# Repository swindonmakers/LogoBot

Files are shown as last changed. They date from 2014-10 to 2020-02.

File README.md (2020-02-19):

LogoBot
=======

Cheap, extensible mobile robot design based on Arduino - inspired by Mirobot and others.  Many of the parts are 3D printed, using a tool-less pin system to connect to the base plate.  The non-printable *vitamins* are low-cost, common and globally available.

See the [Assembly Guides](http://rawgit.com/swindonmakers/LogoBot/master/hardware/docs/index.htm) for easy to follow build instructions and links to the printable STLs.

Developed by the Swindon Makerspace (UK) - see [LogoBot wiki page](https://github.com/swindonmakers/snhack.github.io/wiki/LogoBot) and [related Google Groups thread](https://groups.google.com/d/topic/swindon-hackspace/0EO_l_R9aW0/discussion)

Various photos of LogoBot builds can be found on the [Flickr group](https://www.flickr.com/groups/logobot/), please contribute if you build one!  Videos are collated in the [LogoBot youtube playlist](https://www.youtube.com/playlist?list=PLYuoVOMOzIhp9adQuXN-J07fskV5hSPBj).

Two of the variants are shown below - the basic design and the Scribbler variant that includes a pen lift:

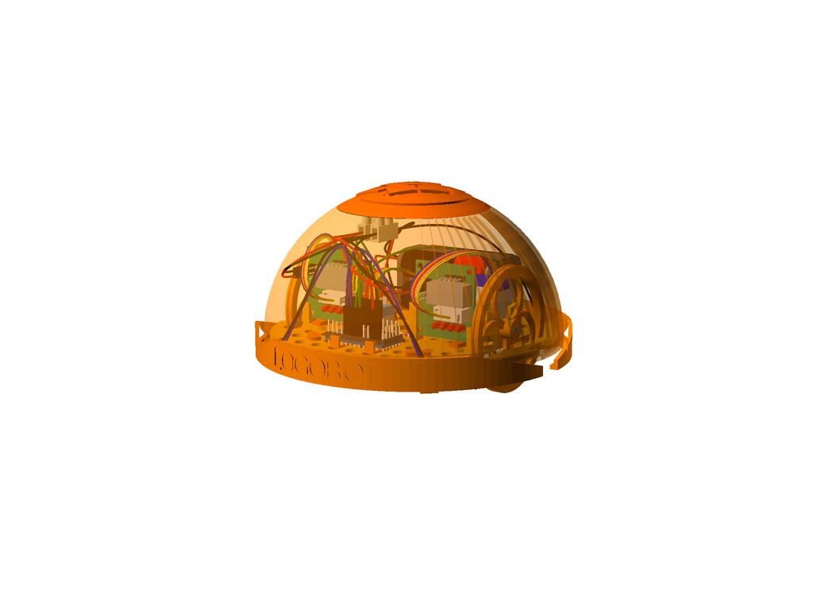
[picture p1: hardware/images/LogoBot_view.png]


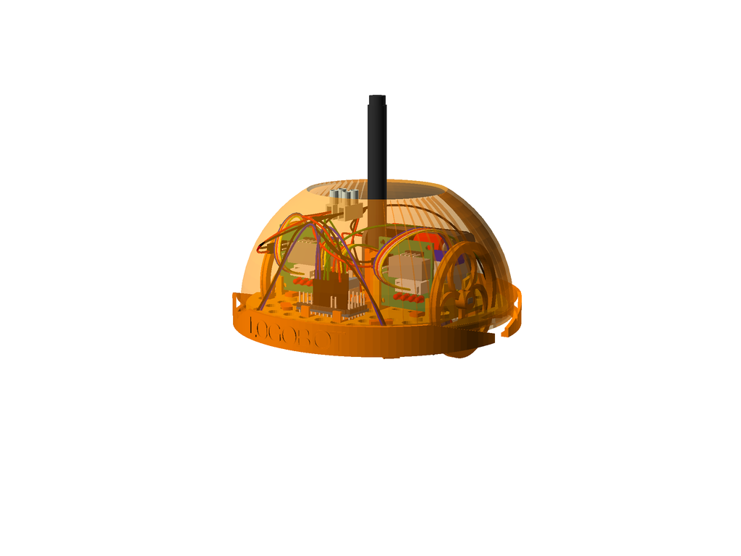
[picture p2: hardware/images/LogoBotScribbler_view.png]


Design Principles
-----------------

* Help teach electronics, programming, 3D design and 3D printing (both to ourselves and others)
* Highly interactive - to attract/hold attention
* Cheap (Total BOM <£20)
* Suitable for ages 6 - 100
* Simplicity is key - all parts/functionality must be easy to explain and understandable by 6-yr olds
* Solderless (where practical)
* Extensible - more sensors, more functionality
* Personalisable - we don't want lots of bland, generic little robots
* Include a Logo interpreter - as per it's namesake :)

File Structure
--------------

* hardware - all OpenSCAD models, and will contains electronic models in the future (e.g. PCB layout)
* software - firmwares and host implementations

Contributions
-------------

Development planning will be coordinated through the normal Wednesday meetings (i.e. who is working on what).  All project members will be given write access to the repo.

Design
------

The rest of this Wiki page is dedicated to design discussion, collected ideas, etc.  For the latest designs, guides and printable STLs, please refer to the [github site](https://github.com/swindonmakers/LogoBot).

Having discussed a variety configurations, we've settled on the following starter design:

* 2-wheels (stepper driven) with caster(s) - arranged as per traditional Turtle bot
* Front and rear bumpers, each connected to a pair of microswitches - users can choose to remap these switches to control behaviours and/or use them as bump switches
* An RGD LED to give the robot character, located near the top/centre of the robot
* A piezo sounder for audio feedback (R2D2 style noises?)

Scribbler
---------

The first standard extension will include a pen lift and WIFI module, permitting remote control from a phone or tablet using a LOGO command set.

* Central pen with micro-servo lift
* ESP8266-01 Wifi module

Other Extensions / Optional Extras
----------------------------------
* Bluetooth UART - for cable-free programming, inter-bot comms, host interface, etc
* Serial RGB LED (to reduce pin count)
* IR Reflectance sensors - for collision avoidance, cliff detection, line following, following behaviour, etc
* IR transceiver - for interaction with TV remotes and/or other robots
* Ultrasonic distance sensors - for collision avoidance, following behaviour, etc
* Speaker - for complex audio playback (e.g. WAV, MP3)
* Microphone(s) - for sound following/localisation and/or voice recognition/recording
* Light Sensors (LDR,etc) - following behaviour, etc
* Tilt sensor - for "I've fallen over" behaviour, etc

Customised Shell Ideas
----------------------
Although the reference design will include a basic dome shell, we really want makers to customise their LogoBot, and a custom shell is a quick way to make a big impression!  

Please add suggestions below, and if you start developing a design, then put your name in the Developer column and be sure to include a link to the source files (e.g. OpenSCAD file) - if there's lots of related information (pictures, etc), then create a wiki page for the design.

| Title | Developer | Link to Source | Notes |
| --- | --- | --- | --- |
| R2D2 | Jamie | | Just his head?  or perhaps a basic body as well? Matching program mode that drives piezo/speaker and adds R2 flourishes to movement (such as taking the 270° turn instead of 90°) |
| Dalek | | | Add a servo for the probiscus? | 
| Pumpkin | | | Halloween fun, with glowing eyes? |
| Lego Base | Damian | See Optional Extras | A lego plate lid to fit any of the standard shells |

Pin Assignments
---------------
First draft of pin assignments...  uses all the normal pins!

Pin(s) | Assignment
:----: | ----------
0-1    | Left spare for later addition of WIFI or Bluetooth UART
2-5    | Left stepper driver
6-9    | Right stepper driver
10     | Piezo sounder
11-13  | RGB LED
A0-A3  | Microswitches - Front Left, Front Right, Back Left, Back Right
|
A4-A7  | Spare headers, not usable on the breadboard

***A4-A7 are additional analog pins, not located at the edge of the board.***

See Also
--------
[OpenSCAD for Machine Design](https://github.com/swindonmakers/wiki/wiki/OpenSCAD-for-Machine-Design)

References
----------
* [Mirobot.io](http://mirobot.io/)
* [ProtoBot](http://www.thingiverse.com/thing:18264)
* [ScoutBot](http://www.thingiverse.com/thing:13042)
* [MiniSkybot](http://www.thingiverse.com/thing:7989)

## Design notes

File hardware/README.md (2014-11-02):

LogoBot Hardware
================

File Structure
--------------

**This Directory**

* LogoBot.scad - the complete reference robot design, open this in OpenSCAD to view the completed model

**Sub Directories**

* assemblies - contains the scad files that describe all the printable parts and sub-assemblies of LogoBot
* docs - assembly guides
* config - global scad configuration files
* printedparts - all printed parts
* utils - utility libraries to make modelling parts easier (e.g. extended shape libraries)
* vitamins - models of various non-printable vitamins (e.g. motors, switches, nuts, bolts)

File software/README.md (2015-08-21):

LogoBot Software
================

Contains the source for Arduino firmwares, ESP8266 firmwares and other bits (like the LogoBot Simulator)

File Structure
--------------
* [firmware](firmware) - contains the Arduino and ESP8266 firmwares and supporting libraries
* [simulator](simulator) - the web-based LogoBot Simulator

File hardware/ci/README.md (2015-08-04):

# CI Scripts

## Overview

The /hardware/ci directory contains all of the continuous integration scripts for the hardware portion of the project.

To build all files within the project:

1. Open a terminal and change to the /hardware/ci directory
2. Run: python build.py  (or just ./build.py)

### Build Process

The build.py script calls the other scripts in order to:

1. Check machine files (and all included files) for syntax errors
2. Parse the various machine files for BOM information, storing the result in hardware.json
3. Render STL and views for vitamins
4. Render STL and views for printed parts
5. Render views for each assembly step of the various assemblies
6. Render views for each completed machine
7. Generate an assembly guide for each machine, in both markdown and html
8. Generate a documentation index file, also in markdown and html
9. Generate a vitamin catalogue (markdown and html)

The process caches information about the structure of each part, so that only changes are rendered.

### Python Dependencies

You'll need to install the following dependencies to run the full build process:

1. PIL - the Python Image Library - use: pip install pillow
2. Pystache - the Pystache template library - use: pip install pystache

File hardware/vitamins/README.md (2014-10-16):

vitamins
========

This directory contains library modules for non-printable vitamin parts (e.g. motors, switches)

File Structure
--------------

**This Directory**

* PlasticCaster.scad - An example vitamin library that defines a basic plastic caster

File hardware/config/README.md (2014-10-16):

config
======

This directory contains .scad files that hold global configuration settings for the project.  Most of these files require little editing and form part of the machine design pattern.

File Structure
--------------

**This Directory**

* assemblies.scad - A list of included assembly files
* colors.scad - A set of material colors for use in vitamins and assemblies
* config.scad - Master config file, includes all other config files - include this in the machine file (e.g. /LogoBot.scad)
* **machine.scad** - Machine specific variables - this is where all of the LogoBot specific parameters are held
* utils.scad - A list of included utility files
* vitamins.scad - A list of included vitamin files

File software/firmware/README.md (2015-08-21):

# firmware

This directory contains the Arduino and ESP8266 firmwares and supporting libraries.
The source files are well commented and should be fairly self-explanatory.

## Build Notes

To build the various firmwares, set your Arduino IDE Sketchbook path to point to this (firmware) directory (restart required).  The various sketches can then be loaded from the File -> Sketchbook menu.

To easily program the ESP8266 firmwares, you'll need need Arduino IDE v1.6.4 or newer.  Then add ESP support via Board Manager.  Testing has been done using ESP8266-01 modules, but other variants should work as well.

## Contents
--------------
* libraries - various reusable libraries for developing LogoBot firmwares, some 3rd party
* LogoBotBasic - Arduino firmware for the basic LogoBot - start here!
* LogoBotEsp8266 - ESP8266 firmware to complement the LogoBotWifiScribbler firmware
* LogoBotIRSeeker - Arduino firmware for the IR Seeker variant
* LogoBotLineFollower - Arduino firmware for the Line Follower variant
* LogoBotPolarGraph - Arduino firmware for the Polar Graph variant
* LogoBotWifiScribbler - Arduino firmware for the Scribbler variant

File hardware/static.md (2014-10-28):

# Static Analysis Report

## Summary

**Fit to Publish:** Yes

Section    | OK  | Note | Warning | Error
---------- |:---:|:----:|:-------:|:-----:
[Assemblies](#assemblies) | 29  | 0    | 1       | 0    
[Vitamins  ](#vitamins  ) | 44  | 0    | 12      | 0    
**Total**  | **73**  | **0**  | **13**  | **0** 

## Assemblies

File     | OK | Note | Warning | Error
------  | :---:  | :---:  | :---:  | :---: 
[Wheel.scad](#wheelscad) | 6 | 0 | 0 | 0
[MarbleCaster.scad](#marblecasterscad) | 6 | 0 | 0 | 0
[Shell.scad](#shellscad) | 5 | 0 | 1 | 0
[Breadboard.scad](#breadboardscad) | 6 | 0 | 0 | 0
[LogoBot.scad](#logobotscad) | 6 | 0 | 0 | 0
**Total**  | **29**  | **0**  | **1**  | **0** 

### Shell.scad

* **Warnings**
  * 2 supplementary modules do not comply with naming convention (BasicShell_STL, BasicShell_STL_View)

## Vitamins

File     | OK | Note | Warning | Error
------  | :---:  | :---:  | :---:  | :---: 
[ULN2003DriverBoard.scad](#uln2003driverboardscad) | 4 | 0 | 0 | 0
[Marble.scad](#marblescad) | 4 | 0 | 0 | 0
[MicroUSB.scad](#microusbscad) | 3 | 0 | 1 | 0
[LED.scad](#ledscad) | 4 | 0 | 0 | 0
[BatteryPack.scad](#batterypackscad) | 2 | 0 | 2 | 0
[motor.scad](#motorscad) | 1 | 0 | 3 | 0
[Bolt.scad](#boltscad) | 2 | 0 | 2 | 0
[MicroSwitch.scad](#microswitchscad) | 3 | 0 | 1 | 0
[Breadboard.scad](#breadboardscad) | 4 | 0 | 0 | 0
[MicroServo.scad](#microservoscad) | 4 | 0 | 0 | 0
[PlasticCaster.scad](#plasticcasterscad) | 4 | 0 | 0 | 0
[JumperWire.scad](#jumperwirescad) | 4 | 0 | 0 | 0
[ArduinoPro.scad](#arduinoproscad) | 4 | 0 | 0 | 0
[murata-piezos.scad](#murata-piezosscad) | 1 | 0 | 3 | 0
**Total**  | **44**  | **0**  | **12**  | **0** 

### MicroUSB.scad

* **Warnings**
  * Vitamin module name does not match filename

### BatteryPack.scad

* **Warnings**
  * Vitamin module name does not match filename
  * 3 supplementary modules do not comply with naming convention (battery, battery_pack_linear, battery_pack_double)

### motor.scad

* **Warnings**
  * Filename is not in UpperCamelCase
  * Vitamin module name does not match filename
  * 1 supplementary modules do not comply with naming convention (logo_motor)

### Bolt.scad

* **Warnings**
  * Vitamin module name does not match filename
  * 3 supplementary modules do not comply with naming convention (HexHeadScrew, HexHeadBolt, Nut)

### MicroSwitch.scad

* **Warnings**
  * 1 supplementary modules do not comply with naming convention (terminal)

### murata-piezos.scad

* **Warnings**
  * Filename is not in UpperCamelCase
  * Vitamin module name does not match filename
  * 25 supplementary modules do not comply with naming convention (murata_7BB_12_9, murata_7BB_15_6, murata_7BB_20_3, murata_7BB_20_6, murata_7BB_20_6L0, murata_7BB_27_4, murata_7BB_27_4L0, murata_7BB_35_3, murata_7BB_35_3L0, murata_7BB_41_2, murata_7BB_41_2L0, murata_7NB_31R2_1, murata_7BB_20_6C, murata_7BB_20_6CL0, murata_7BB_27_4C, murata_7BB_27_4CL0, murata_7BB_35_3C, murata_7BB_35_3CL0, murata_7BB_41_2C, murata_7BB_41_2CL0, murata_7SB_34R7_3C, murata_7series, murata_PKM12EPYH4002_B0, murata_PKM17EPP_2002_B0, murata_PKM_cyl_type)

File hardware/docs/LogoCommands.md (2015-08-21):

## LogoBot - Logo Command Reference

###  Movement

Command | Example | Description
--- | --- | --- 
FD <dist> | FD 20 | Drive forward 20mm | 
BK <dist> | BK 20 | Drive backwards 20mm | 
LT <ang> | LT 90 | Turn left 90 degrees | 
RT <ang> | RT 45 | Turn right 45 degrees | 
TO <x> <y> | TO 20 45 | Move to position x=20, y=45 |
ARC <x> <y> | ARC 50 50 | Move in an arc to position x=50, y=50 |
CIRC <dia> <dir> | CIRC 100 1 | Move in a circle of radius 100 in an anticlockwise direction (<dir>=1 for anticlockwise, -1 for clockwise) |
CS | CS | "Clear screen" - resets current position to be x=0, y=0 |
ST | ST | Smoothly stop movement |
SE | SE | Emergency stop |

###  Other

Command | Example | Description
--- | --- | --- 
PU | PU | Pen up |
PD | PD | Pen down |
BZ <ms> | BZ 500 | Sound the buzzer for 500 milliseconds |
PF <ms> | PF 500 | Pause for 500 milliseconds |

### Text

Command | Example | Description
--- | --- | --- 
WT <msg> | WT Hello | Writes "Hello" |
FS <size> | FS 20 | Sets font size to 20 (default) |
SIG | SIG | Signs Logobots name |

### Debug

Command | Example | Description
--- | --- | --- 
PQ | PQ | Prints the current command queue to serial console for debugging |

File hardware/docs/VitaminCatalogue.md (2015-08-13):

# Vitamin Catalogue

### Contents
 * [ArduinoPro.scad ](#arduinoproscad)
 * [Battery.scad ](#batteryscad)
 * [BatteryPack.scad ](#batterypackscad)
 * [Breadboard.scad ](#breadboardscad)
 * [ESP8266.scad ](#esp8266scad)
 * [FTDIBreakout.scad ](#ftdibreakoutscad)
 * [HCSR04UltrasonicSensor.scad ](#hcsr04ultrasonicsensorscad)
 * [HookAndLoopTape.scad ](#hookandlooptapescad)
 * [JumperWire.scad ](#jumperwirescad)
 * [LED.scad ](#ledscad)
 * [LineSensor.scad ](#linesensorscad)
 * [Marble.scad ](#marblescad)
 * [MicroServo.scad ](#microservoscad)
 * [MicroSwitch.scad ](#microswitchscad)
 * [MiniToggleSwitch.scad ](#minitoggleswitchscad)
 * [Pen.scad ](#penscad)
 * [ServoHorn.scad ](#servohornscad)
 * [TerminalBlock.scad ](#terminalblockscad)
 * [ULN2003DriverBoard.scad ](#uln2003driverboardscad)
 * [nut.scad ](#nutscad)
 * [screw.scad ](#screwscad)
 * [washer.scad ](#washerscad)

## ArduinoPro.scad

Title | Call | Image
--- | --- | ---
Arduino Pro Mini No Header Pins, no serial pins | `ArduinoPro(type=ArduinoPro_Mini, headerpins=0,serialpins=0)` | Arduino Pro Mini No Header Pins, no serial pins

## Battery.scad

Title | Call | Image
--- | --- | ---
AA Battery | `Battery(Battery_AA)` | AA Battery

## BatteryPack.scad

Title | Call | Image
--- | --- | ---
Battery Pack | `BatteryPack()` | Battery Pack

## Breadboard.scad

Title | Call | Image
--- | --- | ---
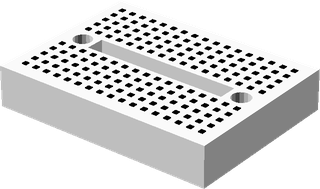
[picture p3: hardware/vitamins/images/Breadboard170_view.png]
Breadboard 170
Breadboard 170 | `Breadboard(Breadboard_170)` | 

## ESP8266.scad

Title | Call | Image
--- | --- | ---
ESP8266 01 | `ESP8266(ESP8266_01)` | ESP8266 01

## FTDIBreakout.scad

Title | Call | Image
--- | --- | ---
FTDI Breakout | `FTDIBreakout()` | FTDI Breakout

## HCSR04UltrasonicSensor.scad

Title | Call | Image
--- | --- | ---
HCSR04 Ultrasonic Sensor | `HCSR04UltrasonicSensor()` | HCSR04 Ultrasonic Sensor

## HookAndLoopTape.scad

Title | Call | Image
--- | --- | ---
Hook and Loop Tape 40x25mm | `HookAndLoopTape(length=40, width=25)` | Hook and Loop Tape 40x25mm

## JumperWire.scad

Title | Call | Image
--- | --- | ---
JumperWire None to None 1pin 100mm | `JumperWire(type=JumperWire_NN1, length=100)` | JumperWire None to None 1pin 100mm
JumperWire Female to None 1pin 100mm | `JumperWire(type=JumperWire_FN1, length=100)` | JumperWire Female to None 1pin 100mm
JumperWire Male to Male 2pin 100mm | `JumperWire(type=JumperWire_MM2, length=100)` | JumperWire Male to Male 2pin 100mm
JumperWire Female to Female 2pin 100mm | `JumperWire(type=JumperWire_FF2, length=100)` | JumperWire Female to Female 2pin 100mm
JumperWire Male to Female 2pin 100mm | `JumperWire(type=JumperWire_MF2, length=100)` | JumperWire Male to Female 2pin 100mm
JumperWire Female to Female 3pin 100mm | `JumperWire(type=JumperWire_FF3, length=100)` | JumperWire Female to Female 3pin 100mm
JumperWire Female to Female 4pin 100mm | `JumperWire(type=JumperWire_FF4, length=100)` | JumperWire Female to Female 4pin 100mm
JumperWire Female to Male 4pin 100mm | `JumperWire(type=JumperWire_FM4, length=100)` | JumperWire Female to Male 4pin 100mm

## LED.scad

Title | Call | Image
--- | --- | ---
3mm LED | `LED(LEDType=LED_3mm)` | 3mm LED
5mm LED | `LED(LEDType=LED_5mm)` | 5mm LED
RGB_5mm LED | `LED(LEDType=LED_RGB_5mm)` | RGB_5mm LED

## LineSensor.scad

Title | Call | Image
--- | --- | ---
Line Sensor | `LineSensor()` | Line Sensor

## Marble.scad

Title | Call | Image
--- | --- | ---
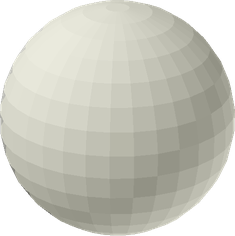
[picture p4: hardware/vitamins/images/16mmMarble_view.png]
16mm Marble
16mm Marble | `Marble(Marble_16mm)` | 

## MicroServo.scad

Title | Call | Image
--- | --- | ---
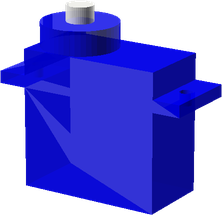
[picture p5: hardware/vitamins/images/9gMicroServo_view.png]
9g Micro Servo
9g Micro Servo | `MicroServo()` | 

## MicroSwitch.scad

Title | Call | Image
--- | --- | ---
MicroSwitch | `MicroSwitch()` | MicroSwitch

## MiniToggleSwitch.scad

Title | Call | Image
--- | --- | ---
SPST6A Mini Toggle Switch | `MiniToggleSwitch(MiniToggleSwitch_SPST6A)` | SPST6A Mini Toggle Switch

## Pen.scad

Title | Call | Image
--- | --- | ---
Fine Line Pen | `Pen()` | Fine Line Pen

## ServoHorn.scad

Title | Call | Image
--- | --- | ---
Servo Horn | `ServoHorn()` | Servo Horn

## TerminalBlock.scad

Title | Call | Image
--- | --- | ---
2 Pole 20A Terminal Block | `TerminalBlock(type=TerminalBlock_20A,poles=2)` | 2 Pole 20A Terminal Block

## ULN2003DriverBoard.scad

Title | Call | Image
--- | --- | ---
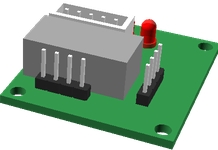
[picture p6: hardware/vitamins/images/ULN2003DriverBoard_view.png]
ULN2003 Driver Board
ULN2003 Driver Board | `ULN2003DriverBoard()` | 

## nut.scad

Title | Call | Image
--- | --- | ---
M2 Nut | `nut(type=M2_nut,nyloc=false,brass=false )` | M2 Nut
M2.5 Nut | `nut(type=M2p5_nut,nyloc=false,brass=false )` | M2.5 Nut
M3 Nut | `nut(type=M3_nut,nyloc=false,brass=false )` | M3 Nut
M4 Nut | `nut(type=M4_nut,nyloc=false,brass=false )` | M4 Nut
M5 Nut | `nut(type=M5_nut,nyloc=false,brass=false )` | M5 Nut
M6 Nut | `nut(type=M6_nut,nyloc=false,brass=false )` | M6 Nut
M6 Half Nut | `nut(type=M6_half_nut,nyloc=false,brass=false )` | M6 Half Nut
M8 Nut | `nut(type=M8_nut,nyloc=false,brass=false )` | M8 Nut
M10 Nut | `nut(type=M10_nut,nyloc=false,brass=false )` | M10 Nut

## screw.scad

Title | Call | Image
--- | --- | ---
M2 pan screw x 20mm | `screw(type=M2_pan_screw,length=20, hob_point=0 )` | M2 pan screw x 20mm
M2.5 pan screw x 20mm | `screw(type=M2p5_pan_screw,length=20, hob_point=0 )` | M2.5 pan screw x 20mm
M2.5 cap screw x 20mm | `screw(type=M2p5_cap_screw,length=20, hob_point=0 )` | M2.5 cap screw x 20mm
M3 cap screw x 20mm | `screw(type=M3_cap_screw,length=20, hob_point=0 )` | M3 cap screw x 20mm
M3 pan screw x 20mm | `screw(type=M3_pan_screw,length=20, hob_point=0 )` | M3 pan screw x 20mm
M3 hex screw x 20mm | `screw(type=M3_hex_screw,length=20, hob_point=0 )` | M3 hex screw x 20mm
M3 grub screw x 20mm | `screw(type=M3_grub_screw,length=20, hob_point=0 )` | M3 grub screw x 20mm
M4 cap screw x 20mm | `screw(type=M4_cap_screw,length=20, hob_point=0 )` | M4 cap screw x 20mm
M4 pan screw x 20mm | `screw(type=M4_pan_screw,length=20, hob_point=0 )` | M4 pan screw x 20mm
M4 hex screw x 20mm | `screw(type=M4_hex_screw,length=20, hob_point=0 )` | M4 hex screw x 20mm
M4 grub screw x 20mm | `screw(type=M4_grub_screw,length=20, hob_point=0 )` | M4 grub screw x 20mm
M5 cap screw x 20mm | `screw(type=M5_cap_screw,length=20, hob_point=0 )` | M5 cap screw x 20mm
M6 cap screw x 20mm | `screw(type=M6_cap_screw,length=20, hob_point=0 )` | M6 cap screw x 20mm
M6 selftap screw T25 x 20mm | `screw(type=M6_selftap_screw,length=20, hob_point=0 )` | M6 selftap screw T25 x 20mm
M8 cap screw x 20mm | `screw(type=M8_cap_screw,length=20, hob_point=0 )` | M8 cap screw x 20mm
M8 hex screw x 20mm | `screw(type=M8_hex_screw,length=20, hob_point=0 )` | M8 hex screw x 20mm
M10 cap screw x 20mm | `screw(type=M10_cap_screw,length=20, hob_point=0 )` | M10 cap screw x 20mm
M5 low profile screw x 20mm | `screw(type=M5_lowprofile_screw,length=20, hob_point=0 )` | M5 low profile screw x 20mm
No2 pan wood screw x 20mm | `screw(type=No2_screw,length=20, hob_point=0 )` | No2 pan wood screw x 20mm
No4 pan wood screw x 20mm | `screw(type=No4_screw,length=20, hob_point=0 )` | No4 pan wood screw x 20mm
No6 pan wood screw x 20mm | `screw(type=No6_screw,length=20, hob_point=0 )` | No6 pan wood screw x 20mm
No6 cs  wood screw x 20mm | `screw(type=No6_cs_screw,length=20, hob_point=0 )` | No6 cs wood screw x 20mm
6-32 pan screw x 20mm | `screw(type=No632_pan_screw,length=20, hob_point=0 )` | 6-32 pan screw x 20mm

## washer.scad

Title | Call | Image
--- | --- | ---
M2 Washer 6x0.5 | `washer(type=M2_washer)` | M2 Washer 6x0.5
M2.5 Washer 5.9x0.5 | `washer(type=M2p5_washer)` | M2.5 Washer 5.9x0.5
M3 Washer 7x0.5 | `washer(type=M3_washer)` | M3 Washer 7x0.5
M3.5 Washer 8x0.5 | `washer(type=M3p5_washer)` | M3.5 Washer 8x0.5
M4 Washer 9x0.8 | `washer(type=M4_washer)` | M4 Washer 9x0.8
M5 Washer 10x1 | `washer(type=M5_washer)` | M5 Washer 10x1
M5 Washer 20x1.4 | `washer(type=M5_penny_washer)` | M5 Washer 20x1.4
M6 Washer 12x1.5 | `washer(type=M6_washer)` | M6 Washer 12x1.5
M8 Washer 17x1.8 | `washer(type=M8_washer)` | M8 Washer 17x1.8
M8 Washer 30x1.5 | `washer(type=M8_penny_washer)` | M8 Washer 30x1.5
M10 Washer 21x2.2 | `washer(type=M10_washer)` | M10 Washer 21x2.2
M3 Rubber Washer 10x1.5 | `washer(type=M3_rubber_washer)` | M3 Rubber Washer 10x1.5

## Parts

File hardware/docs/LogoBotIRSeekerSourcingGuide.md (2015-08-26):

# LogoBot IR Seeker
# Sourcing Guide

### 1x Arduino Pro Mini Pins on top, inc serial pins

Unit Cost | Source | Notes 
--- | --- | --- 
3 | [link](http://www.aliexpress.com/item/CP2102-Module-Pro-Mini-Module-Atmega328-3-3V-8M-For-Arduinoi-Compatible-With-Nano-Free-Shipping/2002847394.html) | Use 3.3v version for wider compatibility and longer battery life

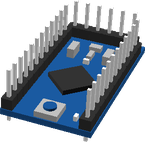
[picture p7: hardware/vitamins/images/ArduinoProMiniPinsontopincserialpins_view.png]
 

### 4x AA Battery

Unit Cost | Source | Notes 
--- | --- | --- 
0.35 | All over the place | Use rechargeables to save cost

 

### 1x Battery Pack

Unit Cost | Source | Notes 
--- | --- | --- 
0.49 | [link](http://www.aliexpress.com/item/Black-Color-2-2-AA-Battery-1-5V-Holder-Storage-Boxes-for-DIY-Experiment-Test-Cascade/1981330624.html) | Any 4xAA pack should work fine, or use 2S LIPO, NIMH, NICAD, etc

 

### 1x Hook and Loop Tape 40x10mm

Unit Cost | Source | Notes 
--- | --- | --- 
0.2 | Hardware store | 

 

### 2x JumperWire Female to Female 4pin 100mm

Unit Cost | Source | Notes 
--- | --- | --- 
0.05 | [link](http://www.ebay.co.uk/itm/40pcs-10cm-Dupont-Female-to-Female-Jumper-Wire-Ribbon-Cable-Pi-Pic-Breadboard-/281423655999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) | Buy in bulk x40

 

### 6x JumperWire Female to None 1pin 100mm

Unit Cost | Source | Notes 
--- | --- | --- 
0.05 |  | Chop end off normal jumper

 

### 4x JumperWire Female to None 1pin 70mm

Unit Cost | Source | Notes 
--- | --- | --- 
0.05 |  | Chop end off normal jumper

 

### 4x JumperWire None to None 1pin 100mm

Unit Cost | Source | Notes 
--- | --- | --- 
0.05 |  | Use any thin multi-strand or solid core wire

 

### 3x JumperWire None to None 1pin 50mm

Unit Cost | Source | Notes 
--- | --- | --- 
0.05 |  | Use any thin multi-strand or solid core wire

 

### 8x 3mm LED

No sources found

 

### 1x 16mm Marble

Unit Cost | Source | Notes 
--- | --- | --- 
0.13 | [link](http://www.ebay.co.uk/itm/NEW-50-16mm-MARBLES-PLUS-ONE-DOBBER-SHOOTER-MARBLE-GREEN-ACK-D60069-/371035484158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) | Buy in bulk x50

 

### 1x 9g Micro Servo

No sources found

 

### 4x MicroSwitch

Unit Cost | Source | Notes 
--- | --- | --- 
0.13 | [link](http://www.ebay.co.uk/itm/15Pcs-SPDT-Straight-Hinge-Lever-Momentary-Micro-Switch-AC125V-1A-/291501876300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) | Buy in bulk x15

 

### 1x SPST6A Mini Toggle Switch

Unit Cost | Source | Notes 
--- | --- | --- 
0.56 | [link](http://www.ebay.co.uk/itm/10x-Mini-Toggle-Switch-6A-SPST-ON-OFF-/251443706793?) | Buy in bulk x10

 

### 1x Servo Horn

No sources found

 

### 1x Sharp2Y0A21

No sources found

 

### 2x 28YBJ48 Stepper Motor

Unit Cost | Source | Notes 
--- | --- | --- 
1.76 | [link](http://www.aliexpress.com/item/5V-Stepper-Motor-28BYJ-48-With-Drive-Test-Module-Board-ULN2003-5-Line-4-Phase-free/1436201179.html) | Comes with driver board

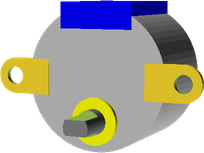
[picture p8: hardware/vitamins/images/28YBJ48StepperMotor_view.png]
 

### 1x 2 Pole 20A Terminal Block

Unit Cost | Source | Notes 
--- | --- | --- 
0.2 | Hardware store | Break off from long terminal strip

 

### 2x ULN2003 Driver Board

Unit Cost | Source | Notes 
--- | --- | --- 
0 |  | Ordered with motor

 

## Summary

### Total Costs

Metric | Value 
--- | --- 
Total Vitamins | 48
Total Cost (cheapest) | 10.97 GBP

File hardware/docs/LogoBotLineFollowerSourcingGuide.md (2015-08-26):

# LogoBot Line Follower
# Sourcing Guide

### 1x Arduino Pro Mini Pins on top, inc serial pins

Unit Cost | Source | Notes 
--- | --- | --- 
3 | [link](http://www.aliexpress.com/item/CP2102-Module-Pro-Mini-Module-Atmega328-3-3V-8M-For-Arduinoi-Compatible-With-Nano-Free-Shipping/2002847394.html) | Use 3.3v version for wider compatibility and longer battery life

 

### 4x AA Battery

Unit Cost | Source | Notes 
--- | --- | --- 
0.35 | All over the place | Use rechargeables to save cost

 

### 1x Battery Pack

Unit Cost | Source | Notes 
--- | --- | --- 
0.49 | [link](http://www.aliexpress.com/item/Black-Color-2-2-AA-Battery-1-5V-Holder-Storage-Boxes-for-DIY-Experiment-Test-Cascade/1981330624.html) | Any 4xAA pack should work fine, or use 2S LIPO, NIMH, NICAD, etc

 

### 1x Hook and Loop Tape 40x10mm

Unit Cost | Source | Notes 
--- | --- | --- 
0.2 | Hardware store | 

 

### 2x JumperWire Female to Female 4pin 100mm

Unit Cost | Source | Notes 
--- | --- | --- 
0.05 | [link](http://www.ebay.co.uk/itm/40pcs-10cm-Dupont-Female-to-Female-Jumper-Wire-Ribbon-Cable-Pi-Pic-Breadboard-/281423655999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) | Buy in bulk x40

 

### 4x JumperWire Female to None 1pin 100mm

Unit Cost | Source | Notes 
--- | --- | --- 
0.05 |  | Chop end off normal jumper

 

### 4x JumperWire Female to None 1pin 70mm

Unit Cost | Source | Notes 
--- | --- | --- 
0.05 |  | Chop end off normal jumper

 

### 2x JumperWire None to None 1pin 100mm

Unit Cost | Source | Notes 
--- | --- | --- 
0.05 |  | Use any thin multi-strand or solid core wire

 

### 3x JumperWire None to None 1pin 50mm

Unit Cost | Source | Notes 
--- | --- | --- 
0.05 |  | Use any thin multi-strand or solid core wire

 

### 8x 3mm LED

No sources found

 

### 2x Line Sensor

No sources found

 

### 1x 16mm Marble

Unit Cost | Source | Notes 
--- | --- | --- 
0.13 | [link](http://www.ebay.co.uk/itm/NEW-50-16mm-MARBLES-PLUS-ONE-DOBBER-SHOOTER-MARBLE-GREEN-ACK-D60069-/371035484158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) | Buy in bulk x50

 

### 1x SPST6A Mini Toggle Switch

Unit Cost | Source | Notes 
--- | --- | --- 
0.56 | [link](http://www.ebay.co.uk/itm/10x-Mini-Toggle-Switch-6A-SPST-ON-OFF-/251443706793?) | Buy in bulk x10

 

### 2x 28YBJ48 Stepper Motor

Unit Cost | Source | Notes 
--- | --- | --- 
1.76 | [link](http://www.aliexpress.com/item/5V-Stepper-Motor-28BYJ-48-With-Drive-Test-Module-Board-ULN2003-5-Line-4-Phase-free/1436201179.html) | Comes with driver board

 

### 1x 2 Pole 20A Terminal Block

Unit Cost | Source | Notes 
--- | --- | --- 
0.2 | Hardware store | Break off from long terminal strip

 

### 2x ULN2003 Driver Board

Unit Cost | Source | Notes 
--- | --- | --- 
0 |  | Ordered with motor

 

## Summary

### Total Costs

Metric | Value 
--- | --- 
Total Vitamins | 39
Total Cost (cheapest) | 10.25 GBP

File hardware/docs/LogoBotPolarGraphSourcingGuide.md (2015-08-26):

# LogoBot Polar Graph
# Sourcing Guide

### 1x Arduino Pro Mini Pins on top, inc serial pins

Unit Cost | Source | Notes 
--- | --- | --- 
3 | [link](http://www.aliexpress.com/item/CP2102-Module-Pro-Mini-Module-Atmega328-3-3V-8M-For-Arduinoi-Compatible-With-Nano-Free-Shipping/2002847394.html) | Use 3.3v version for wider compatibility and longer battery life

 

### 8x 3mm LED

No sources found

 

### 3x 16mm Marble

Unit Cost | Source | Notes 
--- | --- | --- 
0.13 | [link](http://www.ebay.co.uk/itm/NEW-50-16mm-MARBLES-PLUS-ONE-DOBBER-SHOOTER-MARBLE-GREEN-ACK-D60069-/371035484158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) | Buy in bulk x50

 

### 1x 9g Micro Servo

No sources found

 

### 1x Fine Line Pen

No sources found

 

### 1x Servo Horn

No sources found

 

### 2x 28YBJ48 Stepper Motor

Unit Cost | Source | Notes 
--- | --- | --- 
1.76 | [link](http://www.aliexpress.com/item/5V-Stepper-Motor-28BYJ-48-With-Drive-Test-Module-Board-ULN2003-5-Line-4-Phase-free/1436201179.html) | Comes with driver board

 

### 2x ULN2003 Driver Board

Unit Cost | Source | Notes 
--- | --- | --- 
0 |  | Ordered with motor

 

### 4x No6 cs  wood screw x 20mm

No sources found

 

## Summary

### Total Costs

Metric | Value 
--- | --- 
Total Vitamins | 23
Total Cost (cheapest) | 6.91 GBP

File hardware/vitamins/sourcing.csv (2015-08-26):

Vitamin | Cost | Source | Notes
Arduino Pro Mini Pins on top, inc serial pins | 3 | http://www.aliexpress.com/item/CP2102-Module-Pro-Mini-Module-Atmega328-3-3V-8M-For-Arduinoi-Compatible-With-Nano-Free-Shipping/2002847394.html | Use 3.3v version for wider compatibility and longer battery life
AA Battery | 0.35 | All over the place | Use rechargeables to save cost
Battery Pack | 0.49 | http://www.aliexpress.com/item/Black-Color-2-2-AA-Battery-1-5V-Holder-Storage-Boxes-for-DIY-Experiment-Test-Cascade/1981330624.html | Any 4xAA pack should work fine, or use 2S LIPO, NIMH, NICAD, etc
Hook and Loop Tape 40x10mm | 0.2 | Hardware store
JumperWire Female to Female 4pin 100mm | 0.05 | http://www.ebay.co.uk/itm/40pcs-10cm-Dupont-Female-to-Female-Jumper-Wire-Ribbon-Cable-Pi-Pic-Breadboard-/281423655999 | Buy in bulk x40
JumperWire Female to None 1pin 100mm | 0.05 |  | Chop end off normal jumper
JumperWire Female to None 1pin 70mm | 0.05 |  | Chop end off normal jumper
JumperWire None to None 1pin 100mm | 0.05 |  | Use any thin multi-strand or solid core wire
JumperWire None to None 1pin 50mm | 0.05 |  | Use any thin multi-strand or solid core wire
16mm Marble | 0.13 | http://www.ebay.co.uk/itm/NEW-50-16mm-MARBLES-PLUS-ONE-DOBBER-SHOOTER-MARBLE-GREEN-ACK-D60069-/371035484158 | Buy in bulk x50
MicroSwitch | 0.13 | http://www.ebay.co.uk/itm/15Pcs-SPDT-Straight-Hinge-Lever-Momentary-Micro-Switch-AC125V-1A-/291501876300 | Buy in bulk x15
SPST6A Mini Toggle Switch | 0.56 | http://www.ebay.co.uk/itm/10x-Mini-Toggle-Switch-6A-SPST-ON-OFF-/251443706793? | Buy in bulk x10
28YBJ48 Stepper Motor | 1.76 | http://www.aliexpress.com/item/5V-Stepper-Motor-28BYJ-48-With-Drive-Test-Module-Board-ULN2003-5-Line-4-Phase-free/1436201179.html | Comes with driver board
2 Pole 20A Terminal Block | 0.2 | Hardware store | Break off from long terminal strip
ULN2003 Driver Board | 0 |  | Ordered with motor

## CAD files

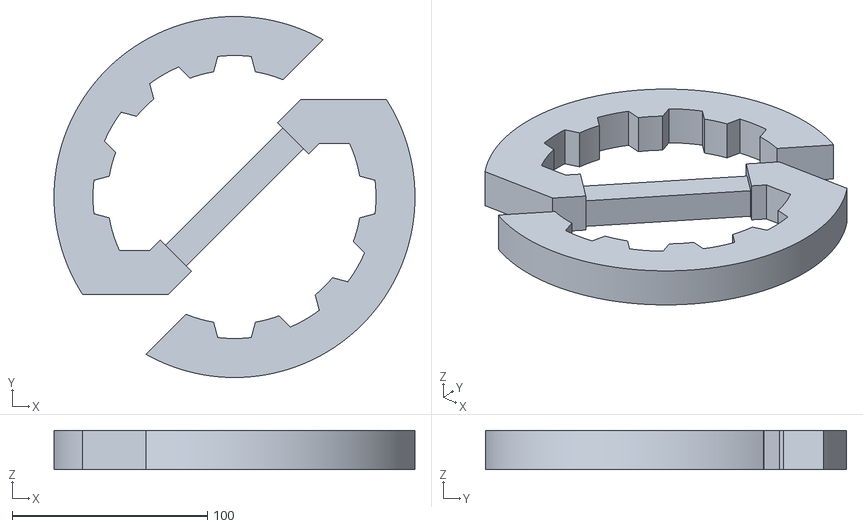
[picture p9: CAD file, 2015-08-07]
hardware/printedparts/snhack_logo_s.stl
185.0 x 185.0 x 20.0

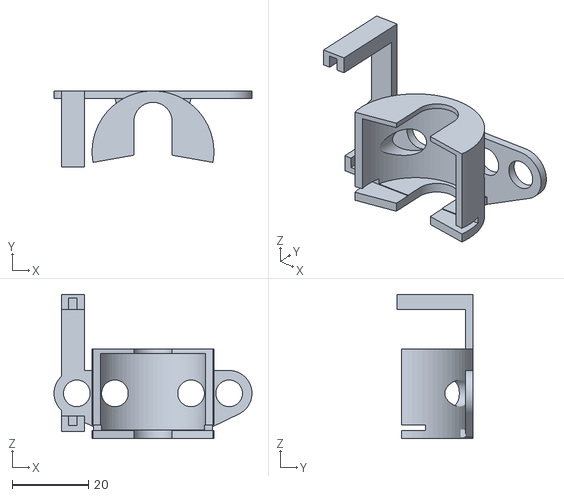
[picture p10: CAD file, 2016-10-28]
hardware/printedparts/stl/LeftMotorClip.stl
52.0 x 20.0 x 37.9

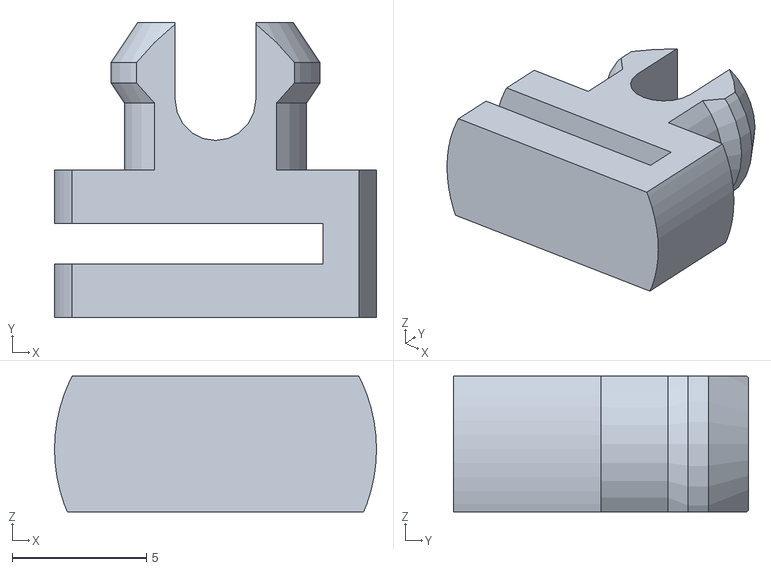
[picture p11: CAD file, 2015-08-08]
hardware/sandbox/stl/PinsCableClipDev.stl
12.0 x 11.0 x 5.05

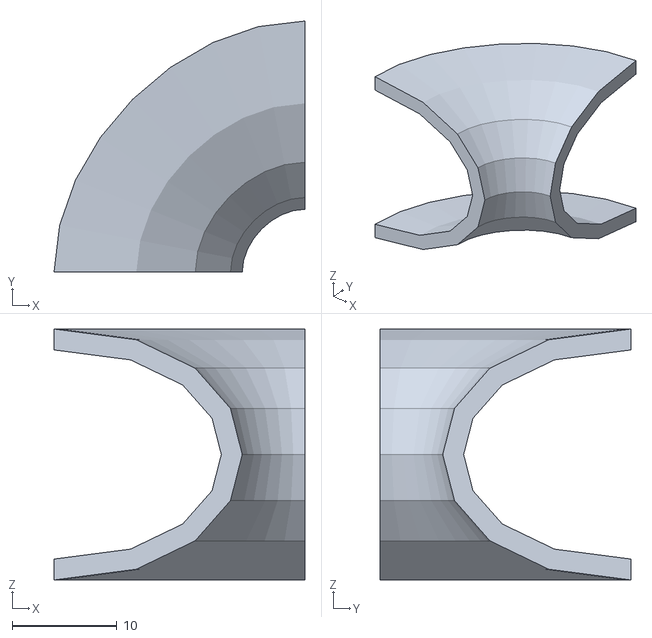
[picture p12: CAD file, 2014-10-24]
hardware/utils/surfacesolids/curve_section.stl
24.0 x 24.0 x 24.0

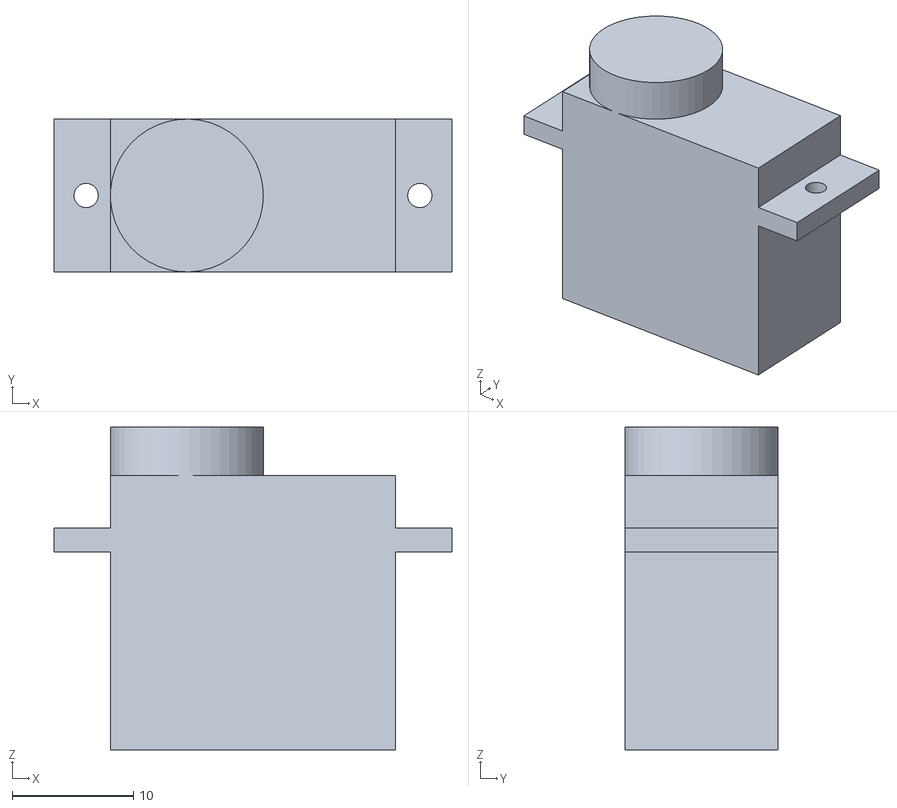
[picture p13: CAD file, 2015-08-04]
hardware/vitamins/stl/MicroServo_Body.stl
32.8 x 12.6 x 26.6

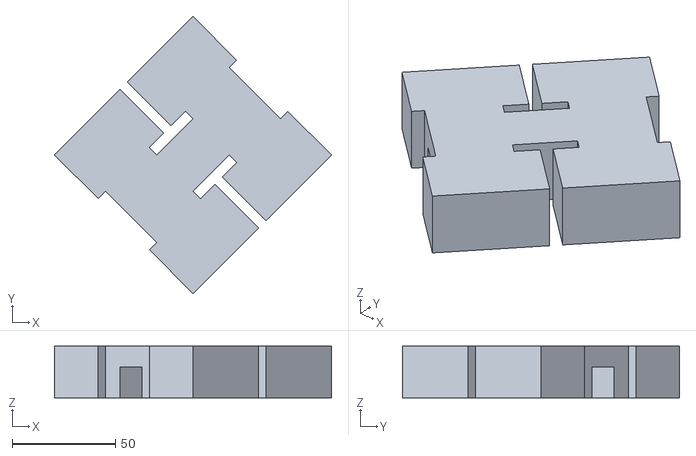
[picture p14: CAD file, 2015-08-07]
hardware/printedparts/snhack_logo_h.stl
134.4 x 134.4 x 25.0

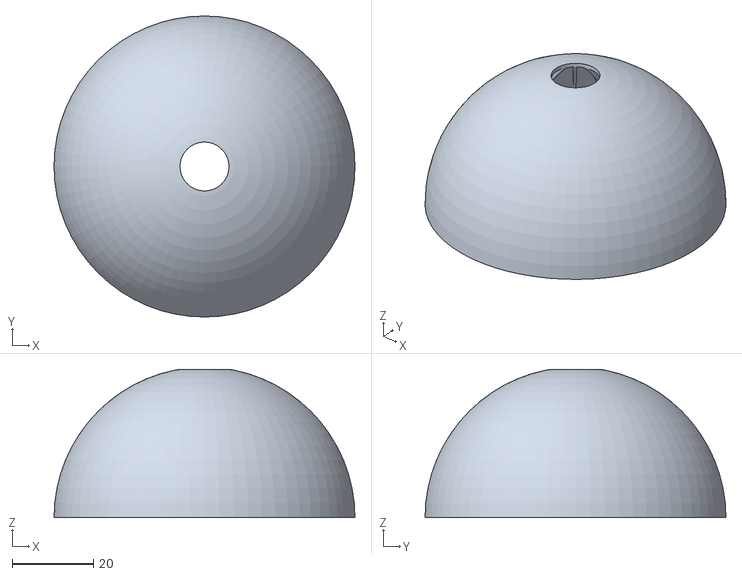
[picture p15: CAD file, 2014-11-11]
hardware/sandbox/stl/supported_dome_70mm.stl
74.0 x 74.0 x 36.5

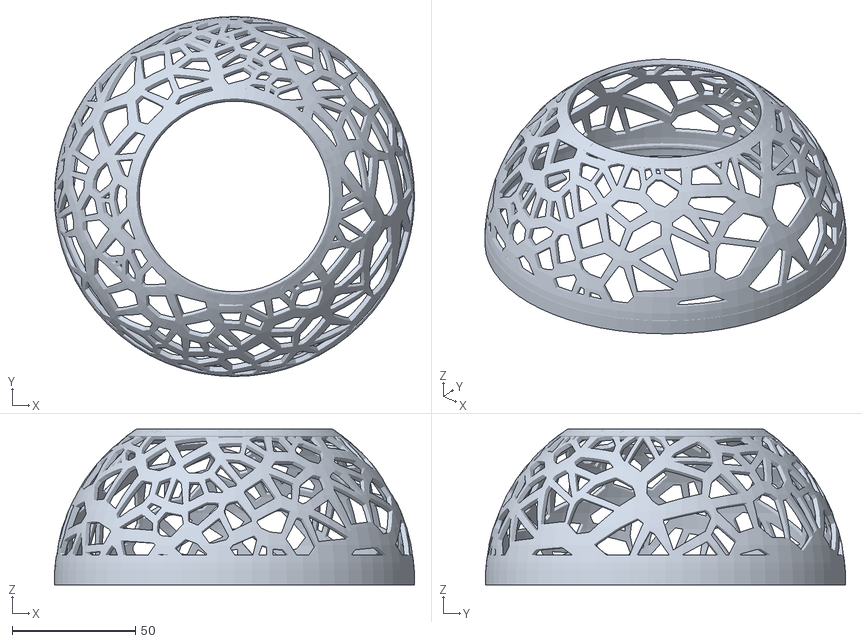
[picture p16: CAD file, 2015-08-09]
hardware/sandbox/VoronoiShell3.stl
146.0 x 146.0 x 63.2

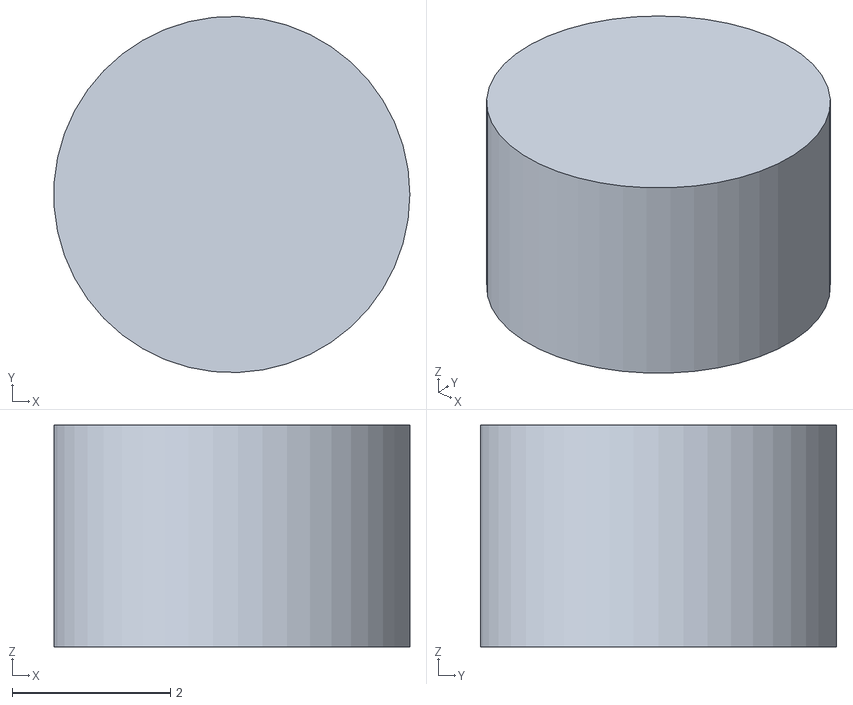
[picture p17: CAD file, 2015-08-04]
hardware/vitamins/stl/MicroServo_Spline.stl
4.49 x 4.50 x 2.80

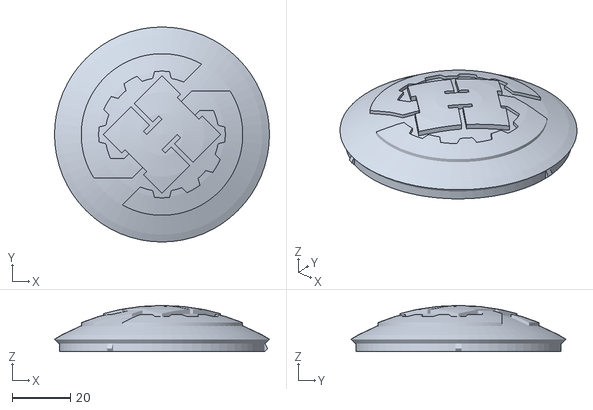
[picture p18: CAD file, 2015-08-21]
hardware/printedparts/stl/Lid.stl
73.9 x 73.9 x 15.9

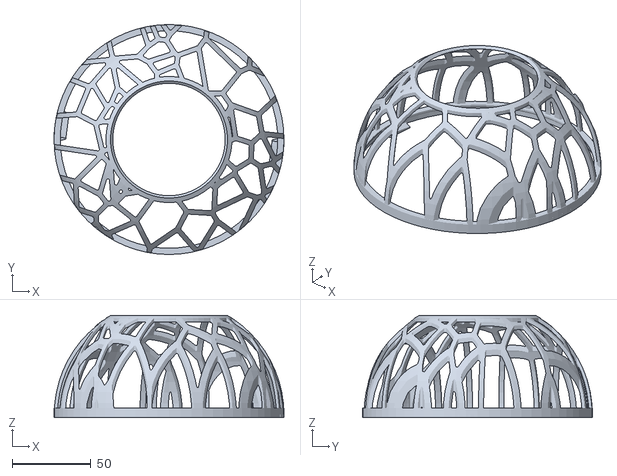
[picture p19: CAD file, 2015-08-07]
hardware/sandbox/VoronoiShell.stl
146.0 x 146.0 x 64.8

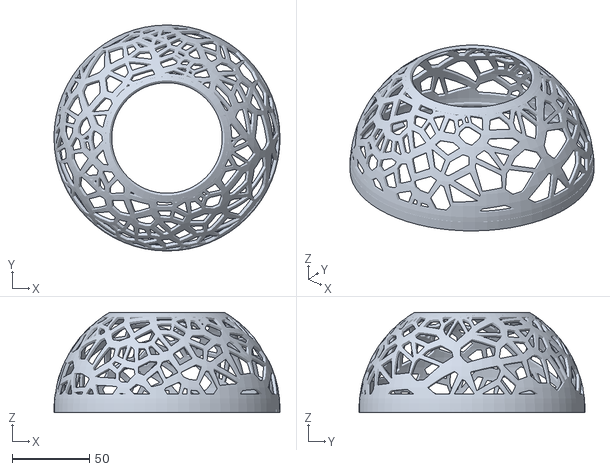
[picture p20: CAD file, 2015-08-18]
hardware/printedparts/stl/VoronoiShellType2.stl
146.0 x 146.0 x 64.8

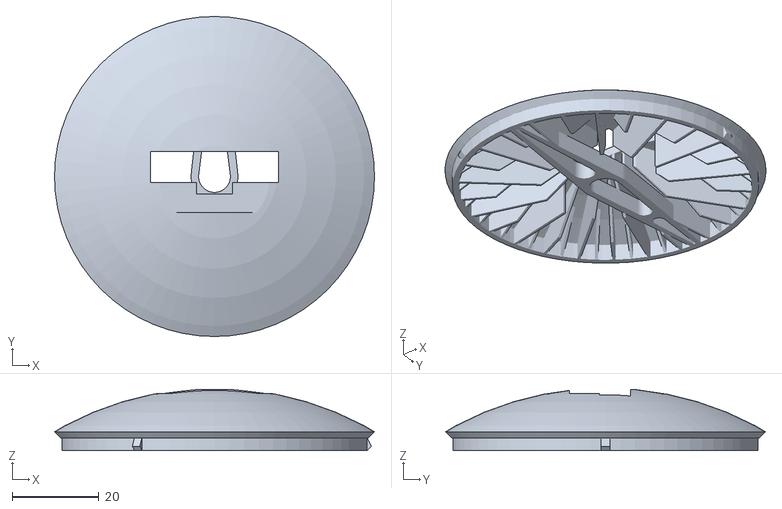
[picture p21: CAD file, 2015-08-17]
hardware/printedparts/stl/LidIR.stl
73.6 x 73.6 x 14.1

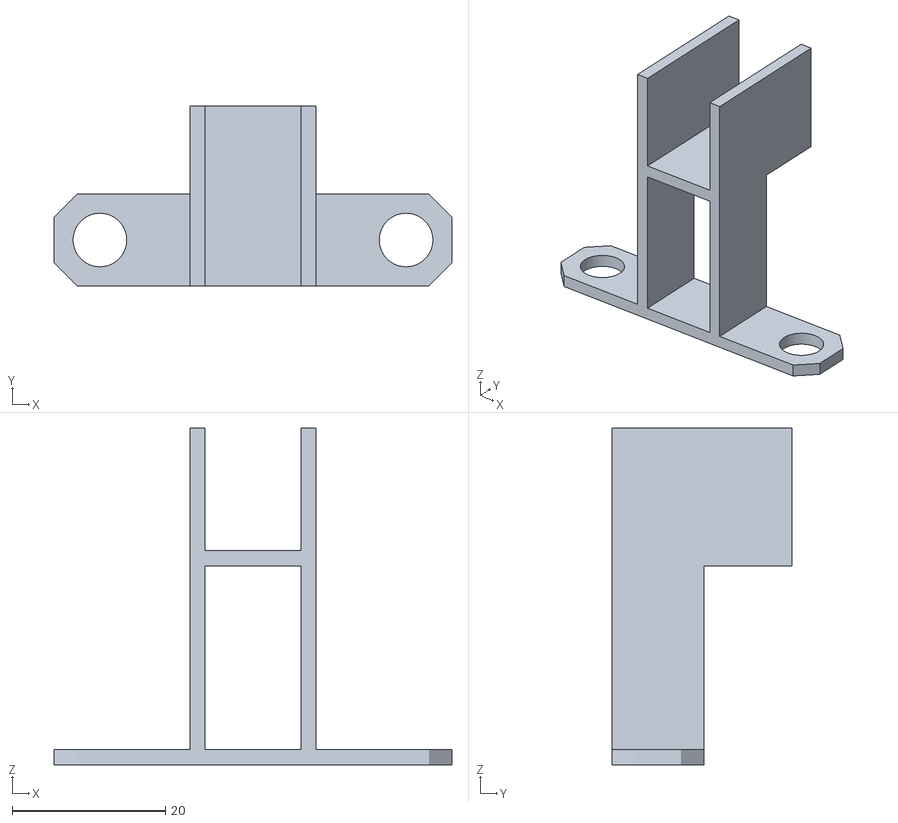
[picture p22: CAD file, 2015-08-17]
hardware/printedparts/stl/IRServoBracket.stl
52.0 x 23.5 x 44.0

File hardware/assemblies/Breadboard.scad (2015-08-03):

/*
	Assembly: BreadboardAssembly
	Breadboard assembly - includes Arduino and fixings

	Local Frame:
		Origin

*/

// Connectors
// ----------

module BreadboardAssembly() {

    assembly("assemblies/Breadboard.scad", "Brain", str("BreadboardAssembly()")) {

        if (DebugCoordinateFrames) frame();

        // debug connectors?
        if (DebugConnectors) {

        }

        // Vitamins
        // --------

        // Breadboard
        Breadboard(Breadboard_170);

        // Arduino
        step(1,
                "Push the Arduino onto the breadboard - make sure you position it correctly,
                 as it's a tight fit with the Robot base!") {
            view(t=[21,17,9], r=[62,0,218], d=316);

            attachWithOffset(Breadboard_Con_Pin(Breadboard_170, along=3, across=7, ang=90), DefConDown, [0,0,3]) {
                ArduinoPro(ArduinoPro_Micro, ArduinoPro_Pins_Opposite);
            }
        }

	}
}

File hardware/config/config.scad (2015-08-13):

//
// Config
//

// Coding-style
// ------------
//
// Global variables are written in UpperCamelCase.
// A logical hierarchy should be indicated using underscores, for example:
//     StepperMotor_Connections_Axle
//
// Global short-hand references should be kept to a minimum to avoid name-collisions



// Global OpenSCAD variables - short-hand!
//
eta = 0.01;                     // small fudge factor to stop CSG barfing on coincident faces.
$fa = 5;
$fs = 0.5;


// Printer specific parameters
//
Perim = 0.5;    // perim extrusion width for 0.2 or 0.3 layer height
Layers = 0.3;
2Perim = 2*Perim;
4Perim = 4*Perim;

// short-hand
perim = Perim;
layers = Layers;
2perim = 2Perim;
4perim = 4Perim;


// Debugging

DebugConnectors = 1;  			// set to 1 to debug, set to 0 for production
DebugCoordinateFrames = 1; 		// set to 1 to debug, set to 0 for production


// Visualisation

// set to true to use STL for printed parts rather than rendering on the fly
UseSTL = false;
STLPath = "../printedparts/stl/";
UseVitaminSTL = true;
VitaminSTL = "../vitamins/stl/";

$Explode  = false;
$ShowStep = 100;

$DefaultViewSize = [400, 300];


// Include all other configuration files

include <holesizes.scad>
include <colors.scad>
include <utils.scad>
include <vitamins.scad>
include <machine.scad>
include <printedparts.scad>
include <assemblies.scad>

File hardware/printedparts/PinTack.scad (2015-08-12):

// Connectors

PinTack_Con_Def = [[0,0,0], [0,0,-1], 0,0,0];


module PinTack_STL(h=10) {

    printedPart(
        "printedparts/PinTack.scad",
        str("Pin Tack H",h),
        str("PinTack_STL(h=",h,")")
    ) {
        markdown("guide","Orient to print on the flat side, no brim.  You may need to sand the flat sides depending on the tolerances of your printer.");

        view(t=[0,0,0],r=[145,135,0],d=130);

        if (DebugCoordinateFrames) frame();
        if (DebugConnectors) {
            connector(PinTack_Con_Def);
        }

        color(Level3PlasticColor) {
            // uses pins.scad library:
            pintack(h=h, bh=2, lh=2, r=PinDiameter/2-0.1);
        }
    }
}

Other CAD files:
hardware/printedparts/stl/RightMotorClip.stl
hardware/printedparts/stl/PinTackH65.stl
hardware/printedparts/stl/LegoLid.stl
hardware/printedparts/stl/CasterHousing.stl
hardware/utils/pins.scad
hardware/LogoBot.scad
hardware/LogoBotIRSeeker.scad
hardware/LogoBotLineFollower.scad
hardware/LogoBotPolarGraph.scad
hardware/LogoBotScribbler.scad
hardware/OptionalExtras.scad
hardware/assemblies/Bumper.scad
hardware/assemblies/Capstan.scad
hardware/assemblies/Gondola.scad
hardware/assemblies/LidIR.scad
hardware/assemblies/LineSensor.scad
hardware/assemblies/LogoBot.scad
hardware/assemblies/LogoBotIRSeeker.scad
hardware/assemblies/LogoBotLineFollower.scad
hardware/assemblies/LogoBotPolarGraph.scad
hardware/assemblies/MarbleCaster.scad
hardware/assemblies/PenLift.scad
hardware/assemblies/Shell.scad
hardware/assemblies/Wheel.scad
hardware/ci/assemblies.scad
hardware/ci/assembly.scad
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

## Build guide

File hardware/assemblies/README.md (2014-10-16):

assemblies
==========

This directory contains the core of the design.  Each file describes a sub-assembly and any associated printed parts.

File Naming Convention
----------------------

Each file should contain a single assembly and it's associated printed parts.
Name files in same case as the assembly module it contains, without the Assembly suffix.

File Structure
--------------

**This Directory**

* LogoBot.scad - the master assembly of the complete robot

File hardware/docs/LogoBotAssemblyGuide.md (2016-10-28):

# LogoBot
# Assembly Guide

view

## Bill of Materials

Make sure you have all of the following parts before you begin.

### Vitamins

Qty | Vitamin | Image
--- | --- | ---
1 | [Arduino Pro Mini Pins on top, inc serial pins]() |  | 
4 | [AA Battery]() |  | 
1 | [Battery Pack]() |  | 
1 | [Hook and Loop Tape 40x10mm]() |  | 
2 | [JumperWire Female to Female 4pin 100mm]() |  | 
6 | [JumperWire Female to None 1pin 100mm]() |  | 
4 | [JumperWire Female to None 1pin 70mm]() |  | 
4 | [JumperWire None to None 1pin 100mm]() |  | 
3 | [JumperWire None to None 1pin 50mm]() |  | 
8 | [3mm LED]() |  | 
1 | [16mm Marble]() |  | 
4 | [MicroSwitch]() |  | 
1 | [SPST6A Mini Toggle Switch]() |  | 
2 | [28YBJ48 Stepper Motor]() |  | 
1 | [2 Pole 20A Terminal Block]() |  | 
2 | [ULN2003 Driver Board]() |  | 

### Printed Parts

Qty | Part Name | Image
--- | --- | ---
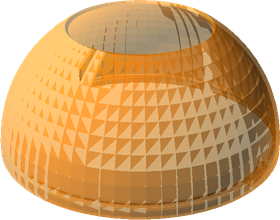
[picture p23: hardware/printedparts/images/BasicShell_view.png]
1 | [Basic Shell](../printedparts/stl/BasicShell.stl) |  | 
2 | [BumperStabiliser](../printedparts/stl/BumperStabiliser.stl) |  | 
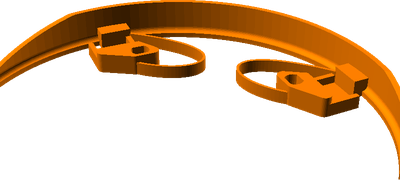
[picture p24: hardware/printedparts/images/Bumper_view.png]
2 | [Bumper](../printedparts/stl/Bumper.stl) |  | 
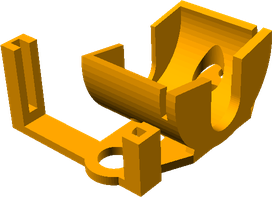
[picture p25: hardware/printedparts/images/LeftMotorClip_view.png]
1 | [Left Motor Clip](../printedparts/stl/LeftMotorClip.stl) |  | 
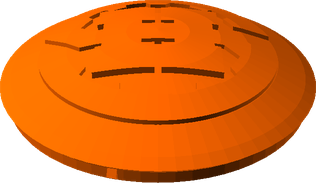
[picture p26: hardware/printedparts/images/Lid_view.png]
1 | [Lid](../printedparts/stl/Lid.stl) |  | 
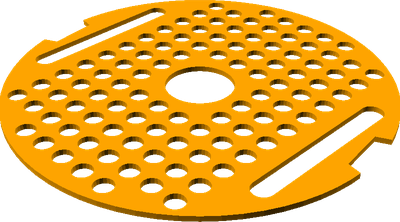
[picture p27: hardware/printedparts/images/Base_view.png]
1 | [Base](../printedparts/stl/Base.stl) |  | 
1 | [Caster Housing](../printedparts/stl/CasterHousing.stl) |  | 
4 | [Pin Tack H14.1](../printedparts/stl/PinTackH141.stl) |  | 
1 | [Pin Tack H6.1](../printedparts/stl/PinTackH61.stl) |  | 
4 | [Pin Tack H7](../printedparts/stl/PinTackH7.stl) |  | 
2 | [Pro Mini Clip](../printedparts/stl/ProMiniClip.stl) |  | 
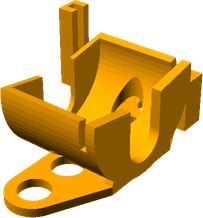
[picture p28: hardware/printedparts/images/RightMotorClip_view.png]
1 | [Right Motor Clip](../printedparts/stl/RightMotorClip.stl) |  | 
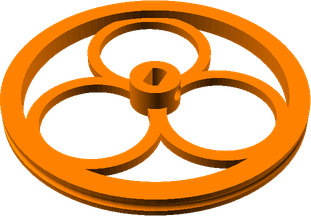
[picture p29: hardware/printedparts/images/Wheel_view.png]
2 | [Wheel](../printedparts/stl/Wheel.stl) |  | 

**Plastic Required**

153.8cm3, 0.19KG,  approx: 2.5 GBP

# Assembly Instructions

## Bumpers (x2)

### Vitamins

Qty | Vitamin | Image
--- | --- | ---
4 | [MicroSwitch]() |  | 

### Printed Parts

Qty | Part Name | Image
--- | --- | ---
2 | [Bumper](../printedparts/stl/Bumper.stl) |  | 

### Assembly Animation

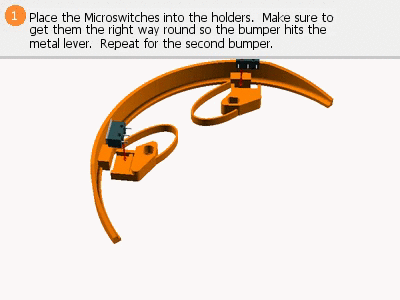
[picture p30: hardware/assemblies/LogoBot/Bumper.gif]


### Assembly Steps

1. Place the Microswitches into the holders.  Make sure to get them the right way round so the bumper hits the metal lever.  Repeat for the second bumper.
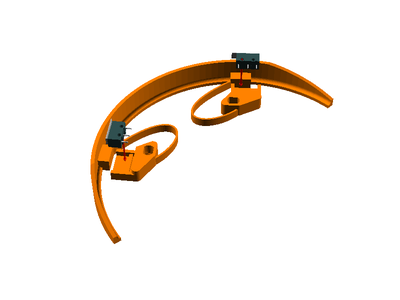
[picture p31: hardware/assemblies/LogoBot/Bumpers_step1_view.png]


## Left Drive Wheel

### Vitamins

Qty | Vitamin | Image
--- | --- | ---
1 | [28YBJ48 Stepper Motor]() |  | 
1 | [ULN2003 Driver Board]() |  | 

### Printed Parts

Qty | Part Name | Image
--- | --- | ---
1 | [Left Motor Clip](../printedparts/stl/LeftMotorClip.stl) |  | 
2 | [Pin Tack H7](../printedparts/stl/PinTackH7.stl) |  | 
1 | [Wheel](../printedparts/stl/Wheel.stl) |  | 

### Assembly Animation

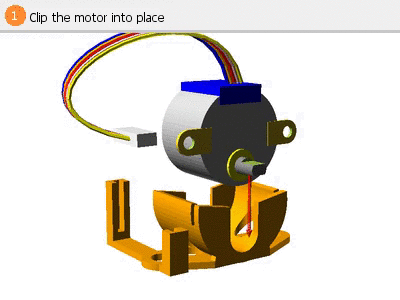
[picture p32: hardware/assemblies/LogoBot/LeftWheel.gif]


### Assembly Steps

1. Clip the motor into place
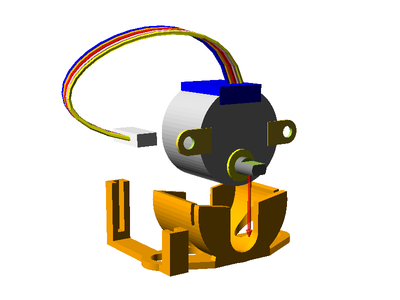
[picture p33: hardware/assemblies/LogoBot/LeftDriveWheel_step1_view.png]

2. Push the pins into the motor clip
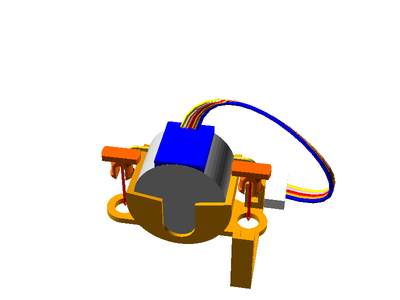
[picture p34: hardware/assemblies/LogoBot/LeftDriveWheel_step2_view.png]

3. Push the wheel onto the motor shaft, then add a rubber band or o-ring to the wheel for extra grip.  You can also add a retaining grub screw if necessary.
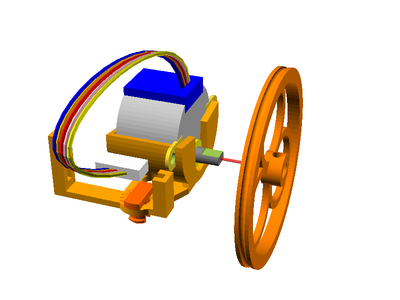
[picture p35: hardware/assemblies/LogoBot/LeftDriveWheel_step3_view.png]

4. Slide the stepper driver into place and plug in the cable for the motor
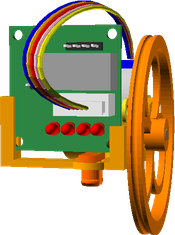
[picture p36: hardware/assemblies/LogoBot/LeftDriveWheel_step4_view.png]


## Right Drive Wheel

### Vitamins

Qty | Vitamin | Image
--- | --- | ---
1 | [28YBJ48 Stepper Motor]() |  | 
1 | [ULN2003 Driver Board]() |  | 

### Printed Parts

Qty | Part Name | Image
--- | --- | ---
2 | [Pin Tack H7](../printedparts/stl/PinTackH7.stl) |  | 
1 | [Right Motor Clip](../printedparts/stl/RightMotorClip.stl) |  | 
1 | [Wheel](../printedparts/stl/Wheel.stl) |  | 

### Assembly Animation

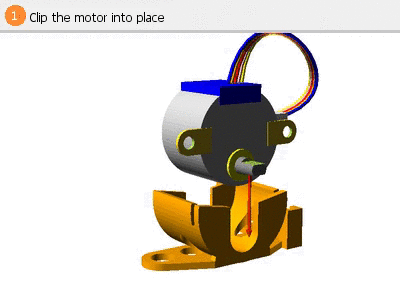
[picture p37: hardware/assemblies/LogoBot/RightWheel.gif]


### Assembly Steps

1. Clip the motor into place
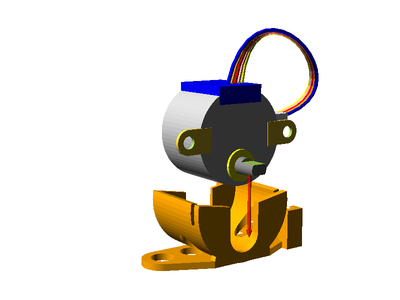
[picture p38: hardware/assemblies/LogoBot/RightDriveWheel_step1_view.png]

2. Push the pins into the motor clip
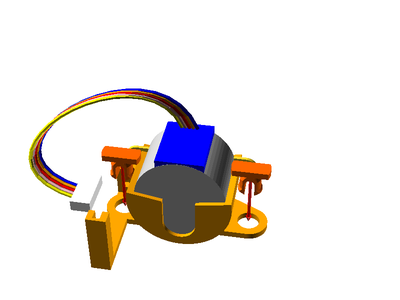
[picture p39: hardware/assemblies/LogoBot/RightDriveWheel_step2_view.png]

3. Push the wheel onto the motor shaft, then add a rubber band or o-ring to the wheel for extra grip.  You can also add a retaining grub screw if necessary.
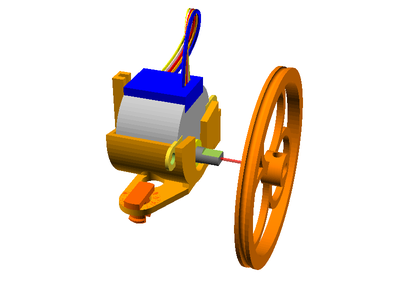
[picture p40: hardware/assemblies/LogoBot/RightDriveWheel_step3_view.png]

4. Slide the stepper driver into place and plug in the cable for the motor
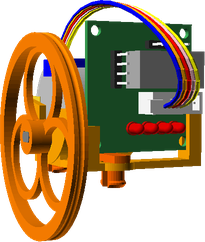
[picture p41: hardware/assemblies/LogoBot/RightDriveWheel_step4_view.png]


## Rear Caster

### Vitamins

Qty | Vitamin | Image
--- | --- | ---
1 | [16mm Marble]() |  | 

### Printed Parts

Qty | Part Name | Image
--- | --- | ---
1 | [Caster Housing](../printedparts/stl/CasterHousing.stl) |  | 

### Assembly Animation

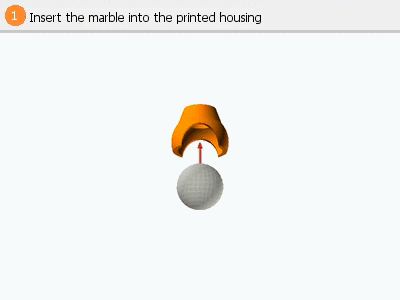
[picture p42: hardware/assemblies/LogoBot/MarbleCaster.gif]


### Assembly Steps

1. Insert the marble into the printed housing
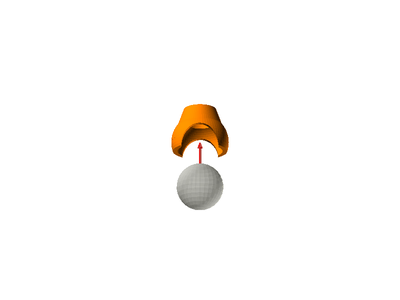
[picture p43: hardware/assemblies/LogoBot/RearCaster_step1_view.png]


## Shell

### Printed Parts

Qty | Part Name | Image
--- | --- | ---
1 | [Basic Shell](../printedparts/stl/BasicShell.stl) |  | 
1 | [Lid](../printedparts/stl/Lid.stl) |  | 

### Assembly Animation

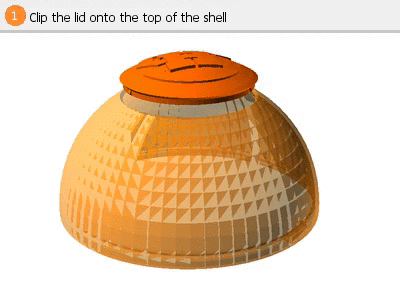
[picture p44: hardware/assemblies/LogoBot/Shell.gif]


### Assembly Steps

1. Clip the lid onto the top of the shell
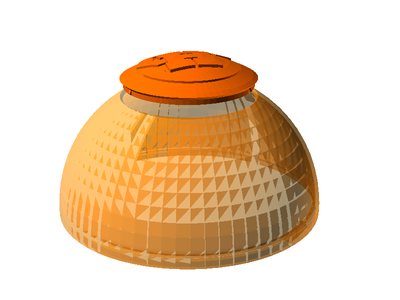
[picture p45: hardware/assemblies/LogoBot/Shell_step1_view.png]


## Final Assembly

### Vitamins

Qty | Vitamin | Image
--- | --- | ---
1 | [Arduino Pro Mini Pins on top, inc serial pins]() |  | 
4 | [AA Battery]() |  | 
1 | [Battery Pack]() |  | 
1 | [Hook and Loop Tape 40x10mm]() |  | 
2 | [JumperWire Female to Female 4pin 100mm]() |  | 
6 | [JumperWire Female to None 1pin 100mm]() |  | 
4 | [JumperWire Female to None 1pin 70mm]() |  | 
4 | [JumperWire None to None 1pin 100mm]() |  | 
3 | [JumperWire None to None 1pin 50mm]() |  | 
1 | [SPST6A Mini Toggle Switch]() |  | 
1 | [2 Pole 20A Terminal Block]() |  | 

### Printed Parts

Qty | Part Name | Image
--- | --- | ---
2 | [BumperStabiliser](../printedparts/stl/BumperStabiliser.stl) |  | 
1 | [Base](../printedparts/stl/Base.stl) |  | 
4 | [Pin Tack H14.1](../printedparts/stl/PinTackH141.stl) |  | 
1 | [Pin Tack H6.1](../printedparts/stl/PinTackH61.stl) |  | 
2 | [Pro Mini Clip](../printedparts/stl/ProMiniClip.stl) |  | 

### Sub-Assemblies

Qty | Name 
--- | --- 
2 | Bumpers
1 | Left Drive Wheel
1 | Right Drive Wheel
1 | Rear Caster
1 | Shell

### Assembly Animation



### Assembly Steps

1. Plug the Pro Mini Clips into the base and then snap the Arduino Pro Mini into them
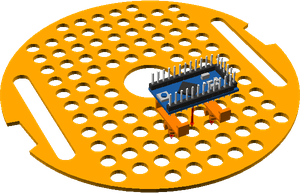
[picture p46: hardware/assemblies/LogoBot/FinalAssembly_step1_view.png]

2. Connect the two bumper assemblies using four of the push pins with flat heads
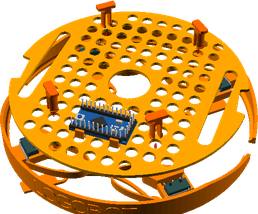
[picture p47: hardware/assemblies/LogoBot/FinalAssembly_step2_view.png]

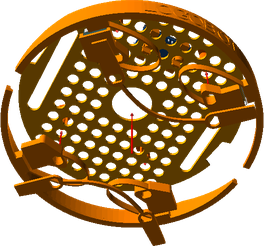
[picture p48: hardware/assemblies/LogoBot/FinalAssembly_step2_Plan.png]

4. Plug the two wheels assemblies into the base
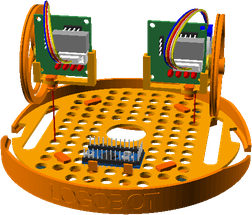
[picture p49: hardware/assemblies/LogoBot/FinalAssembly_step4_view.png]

5. Connect the jumper wires between the motor drivers and the Arduino
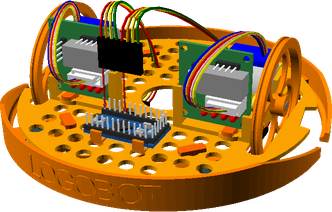
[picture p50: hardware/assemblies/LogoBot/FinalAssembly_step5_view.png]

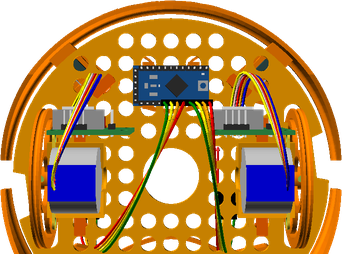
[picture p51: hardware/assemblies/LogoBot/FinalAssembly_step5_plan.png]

6. Fix the power toggle switch into place
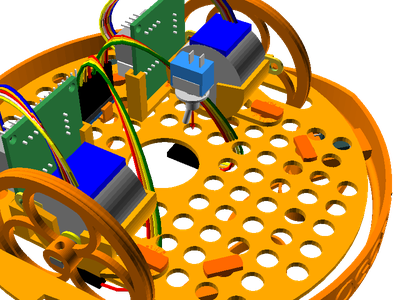
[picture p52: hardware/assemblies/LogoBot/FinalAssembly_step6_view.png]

9. Align the caster assembly with the base, then insert a short pin to lock it to the base
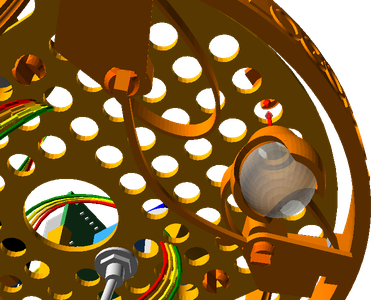
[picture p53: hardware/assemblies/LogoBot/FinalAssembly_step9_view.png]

11. Attach the battery pack with self-adhesive hook and loop tape
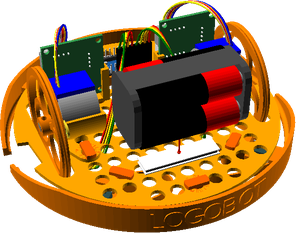
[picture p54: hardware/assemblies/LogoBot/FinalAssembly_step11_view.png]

12. Wire in the terminal block to distribute power
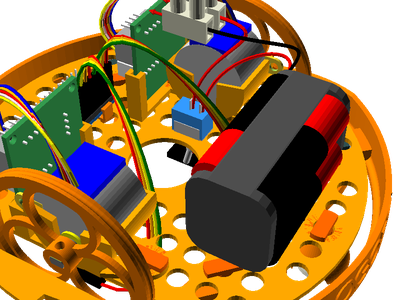
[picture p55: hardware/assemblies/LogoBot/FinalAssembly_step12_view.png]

13. Wire up power to the stepper drivers and Arduino.  Then connect the microswitches to the Arduino. 
            Refer to the following wiring for Arduino pin connections: 
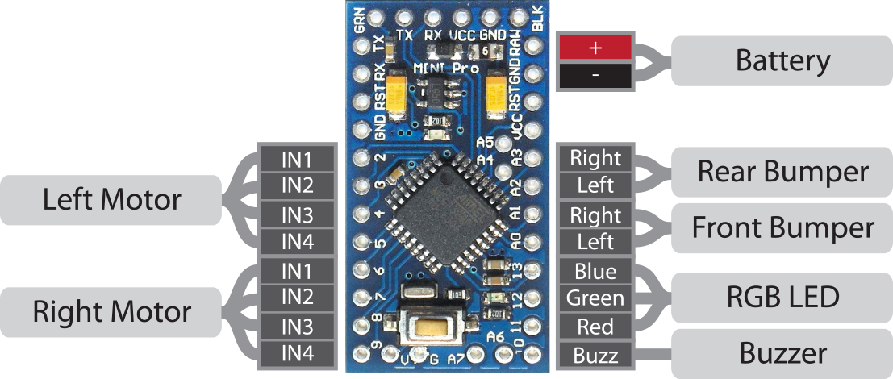
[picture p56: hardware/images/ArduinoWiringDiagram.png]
Arduino Wiring Diagram
            
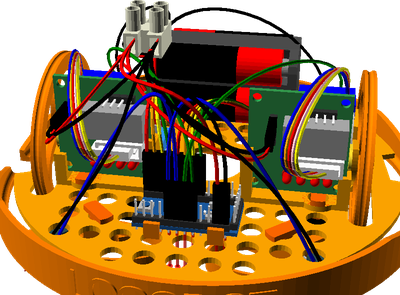
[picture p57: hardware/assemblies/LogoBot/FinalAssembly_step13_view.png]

14. Push the shell down onto the base and twist to lock into place
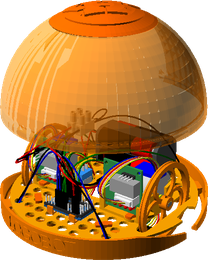
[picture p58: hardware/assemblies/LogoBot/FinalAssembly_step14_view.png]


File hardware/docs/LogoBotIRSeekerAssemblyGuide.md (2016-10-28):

# LogoBot IR Seeker
# Assembly Guide

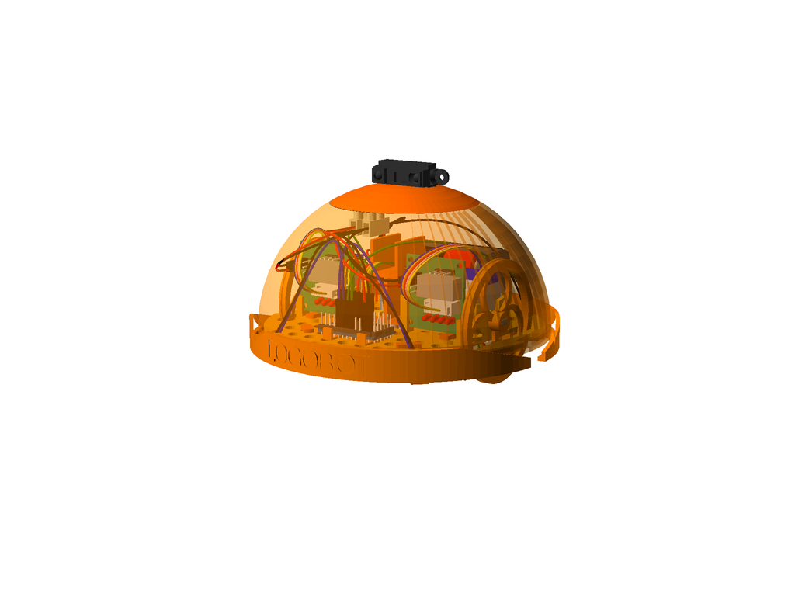
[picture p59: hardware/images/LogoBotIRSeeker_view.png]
view


## Bill of Materials

Make sure you have all of the following parts before you begin.

### Vitamins

Qty | Vitamin | Image
--- | --- | ---
1 | [Arduino Pro Mini Pins on top, inc serial pins]() |  | 
4 | [AA Battery]() |  | 
1 | [Battery Pack]() |  | 
1 | [Hook and Loop Tape 40x10mm]() |  | 
2 | [JumperWire Female to Female 4pin 100mm]() |  | 
6 | [JumperWire Female to None 1pin 100mm]() |  | 
4 | [JumperWire Female to None 1pin 70mm]() |  | 
4 | [JumperWire None to None 1pin 100mm]() |  | 
3 | [JumperWire None to None 1pin 50mm]() |  | 
8 | [3mm LED]() |  | 
1 | [16mm Marble]() |  | 
1 | [9g Micro Servo]() |  | 
4 | [MicroSwitch]() |  | 
1 | [SPST6A Mini Toggle Switch]() |  | 
1 | [Servo Horn]() |  | 
1 | [Sharp2Y0A21]() |  | 
2 | [28YBJ48 Stepper Motor]() |  | 
1 | [2 Pole 20A Terminal Block]() |  | 
2 | [ULN2003 Driver Board]() |  | 

### Printed Parts

Qty | Part Name | Image
--- | --- | ---
1 | [Basic Shell](../printedparts/stl/BasicShell.stl) |  | 
2 | [BumperStabiliser](../printedparts/stl/BumperStabiliser.stl) |  | 
2 | [Bumper](../printedparts/stl/Bumper.stl) |  | 
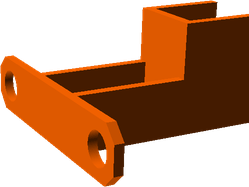
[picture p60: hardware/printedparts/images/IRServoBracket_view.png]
1 | [IR Servo Bracket](../printedparts/stl/IRServoBracket.stl) |  | 
1 | [Left Motor Clip](../printedparts/stl/LeftMotorClip.stl) |  | 
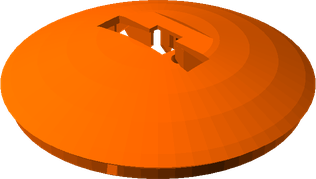
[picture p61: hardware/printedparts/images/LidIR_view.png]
1 | [LidIR](../printedparts/stl/LidIR.stl) |  | 
1 | [Base](../printedparts/stl/Base.stl) |  | 
1 | [Caster Housing](../printedparts/stl/CasterHousing.stl) |  | 
4 | [Pin Tack H14.1](../printedparts/stl/PinTackH141.stl) |  | 
1 | [Pin Tack H6.1](../printedparts/stl/PinTackH61.stl) |  | 
2 | [Pin Tack H6.5](../printedparts/stl/PinTackH65.stl) |  | 
4 | [Pin Tack H7](../printedparts/stl/PinTackH7.stl) |  | 
2 | [Pro Mini Clip](../printedparts/stl/ProMiniClip.stl) |  | 
1 | [Right Motor Clip](../printedparts/stl/RightMotorClip.stl) |  | 
2 | [Wheel](../printedparts/stl/Wheel.stl) |  | 

**Plastic Required**

159.1cm3, 0.2KG,  approx: 2.59 GBP

# Assembly Instructions

## Bumpers (x2)

### Vitamins

Qty | Vitamin | Image
--- | --- | ---
4 | [MicroSwitch]() |  | 

### Printed Parts

Qty | Part Name | Image
--- | --- | ---
2 | [Bumper](../printedparts/stl/Bumper.stl) |  | 

### Assembly Animation



### Assembly Steps

1. Place the Microswitches into the holders.  Make sure to get them the right way round so the bumper hits the metal lever.  Repeat for the second bumper.
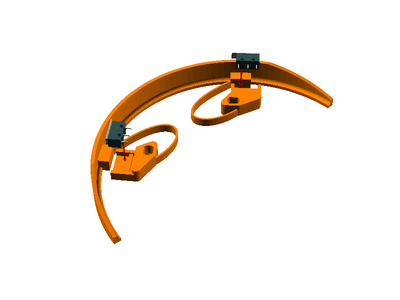
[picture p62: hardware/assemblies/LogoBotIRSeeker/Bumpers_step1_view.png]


## Left Drive Wheel

### Vitamins

Qty | Vitamin | Image
--- | --- | ---
1 | [28YBJ48 Stepper Motor]() |  | 
1 | [ULN2003 Driver Board]() |  | 

### Printed Parts

Qty | Part Name | Image
--- | --- | ---
1 | [Left Motor Clip](../printedparts/stl/LeftMotorClip.stl) |  | 
2 | [Pin Tack H7](../printedparts/stl/PinTackH7.stl) |  | 
1 | [Wheel](../printedparts/stl/Wheel.stl) |  | 

### Assembly Animation



### Assembly Steps

1. Clip the motor into place

2. Push the pins into the motor clip

3. Push the wheel onto the motor shaft, then add a rubber band or o-ring to the wheel for extra grip.  You can also add a retaining grub screw if necessary.

4. Slide the stepper driver into place and plug in the cable for the motor


## Right Drive Wheel

### Vitamins

Qty | Vitamin | Image
--- | --- | ---
1 | [28YBJ48 Stepper Motor]() |  | 
1 | [ULN2003 Driver Board]() |  | 

### Printed Parts

Qty | Part Name | Image
--- | --- | ---
2 | [Pin Tack H7](../printedparts/stl/PinTackH7.stl) |  | 
1 | [Right Motor Clip](../printedparts/stl/RightMotorClip.stl) |  | 
1 | [Wheel](../printedparts/stl/Wheel.stl) |  | 

### Assembly Animation



### Assembly Steps

1. Clip the motor into place

2. Push the pins into the motor clip

3. Push the wheel onto the motor shaft, then add a rubber band or o-ring to the wheel for extra grip.  You can also add a retaining grub screw if necessary.

4. Slide the stepper driver into place and plug in the cable for the motor


## Rear Caster

### Vitamins

Qty | Vitamin | Image
--- | --- | ---
1 | [16mm Marble]() |  | 

### Printed Parts

Qty | Part Name | Image
--- | --- | ---
1 | [Caster Housing](../printedparts/stl/CasterHousing.stl) |  | 

### Assembly Animation



### Assembly Steps

1. Insert the marble into the printed housing


## Lid IR

### Vitamins

Qty | Vitamin | Image
--- | --- | ---
1 | [9g Micro Servo]() |  | 
1 | [Servo Horn]() |  | 
1 | [Sharp2Y0A21]() |  | 

### Printed Parts

Qty | Part Name | Image
--- | --- | ---
1 | [LidIR](../printedparts/stl/LidIR.stl) |  | 

### Assembly Steps

1. Push fit the micro servo horn into the base of the lid

2. Fit the distance sensor into the top of the shell, threading the cable down through the lid


## Final Assembly

### Vitamins

Qty | Vitamin | Image
--- | --- | ---
1 | [Arduino Pro Mini Pins on top, inc serial pins]() |  | 
4 | [AA Battery]() |  | 
1 | [Battery Pack]() |  | 
1 | [Hook and Loop Tape 40x10mm]() |  | 
2 | [JumperWire Female to Female 4pin 100mm]() |  | 
6 | [JumperWire Female to None 1pin 100mm]() |  | 
4 | [JumperWire Female to None 1pin 70mm]() |  | 
4 | [JumperWire None to None 1pin 100mm]() |  | 
3 | [JumperWire None to None 1pin 50mm]() |  | 
1 | [SPST6A Mini Toggle Switch]() |  | 
1 | [2 Pole 20A Terminal Block]() |  | 

### Printed Parts

Qty | Part Name | Image
--- | --- | ---
1 | [Basic Shell](../printedparts/stl/BasicShell.stl) |  | 
2 | [BumperStabiliser](../printedparts/stl/BumperStabiliser.stl) |  | 
1 | [IR Servo Bracket](../printedparts/stl/IRServoBracket.stl) |  | 
1 | [Base](../printedparts/stl/Base.stl) |  | 
4 | [Pin Tack H14.1](../printedparts/stl/PinTackH141.stl) |  | 
1 | [Pin Tack H6.1](../printedparts/stl/PinTackH61.stl) |  | 
2 | [Pin Tack H6.5](../printedparts/stl/PinTackH65.stl) |  | 
2 | [Pro Mini Clip](../printedparts/stl/ProMiniClip.stl) |  | 

### Sub-Assemblies

Qty | Name 
--- | --- 
2 | Bumpers
1 | Left Drive Wheel
1 | Right Drive Wheel
1 | Rear Caster
1 | Lid IR

### Assembly Steps

1. Plug the Pro Mini Clips into the base and then snap the Arduino Pro Mini into them

2. Connect the two bumper assemblies using four of the push pins with flat heads


4. Plug the two wheels assemblies into the base

5. Connect the jumper wires between the motor drivers and the Arduino


6. Fix the power toggle switch into place

9. Align the caster assembly with the base, then insert a short pin to lock it to the base

10. Fix the servo bracket assembly into place using two pins

11. Attach the battery pack with self-adhesive hook and loop tape

12. Wire in the terminal block to distribute power

13. Wire up power to the stepper drivers and Arduino.  Then connect the microswitches to the Arduino. 
            Refer to the following wiring for Arduino pin connections: 
            Arduino Wiring Diagram

14. Push the shell down onto the base and twist to lock into place

15. Push fit the servo into the bracket, thereby fixing the lid in place


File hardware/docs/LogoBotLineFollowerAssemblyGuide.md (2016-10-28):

# LogoBot Line Follower
# Assembly Guide

view

## Bill of Materials

Make sure you have all of the following parts before you begin.

### Vitamins

Qty | Vitamin | Image
--- | --- | ---
1 | [Arduino Pro Mini Pins on top, inc serial pins]() |  | 
4 | [AA Battery]() |  | 
1 | [Battery Pack]() |  | 
1 | [Hook and Loop Tape 40x10mm]() |  | 
2 | [JumperWire Female to Female 4pin 100mm]() |  | 
4 | [JumperWire Female to None 1pin 100mm]() |  | 
4 | [JumperWire Female to None 1pin 70mm]() |  | 
2 | [JumperWire None to None 1pin 100mm]() |  | 
3 | [JumperWire None to None 1pin 50mm]() |  | 
8 | [3mm LED]() |  | 
2 | [Line Sensor]() |  | 
1 | [16mm Marble]() |  | 
1 | [SPST6A Mini Toggle Switch]() |  | 
2 | [28YBJ48 Stepper Motor]() |  | 
1 | [2 Pole 20A Terminal Block]() |  | 
2 | [ULN2003 Driver Board]() |  | 

### Printed Parts

Qty | Part Name | Image
--- | --- | ---
1 | [Left Motor Clip](../printedparts/stl/LeftMotorClip.stl) |  | 
1 | [Line Sensor Holder](../printedparts/stl/LineSensorHolder.stl) |  | 
1 | [Base](../printedparts/stl/Base.stl) |  | 
1 | [Caster Housing](../printedparts/stl/CasterHousing.stl) |  | 
1 | [Pin Tack H6.1](../printedparts/stl/PinTackH61.stl) |  | 
5 | [Pin Tack H7](../printedparts/stl/PinTackH7.stl) |  | 
1 | [Right Motor Clip](../printedparts/stl/RightMotorClip.stl) |  | 
2 | [Wheel](../printedparts/stl/Wheel.stl) |  | 

**Plastic Required**

46.0cm3, 0.06KG,  approx: 0.75 GBP

# Assembly Instructions

## Line Sensor

### Vitamins

Qty | Vitamin | Image
--- | --- | ---
2 | [Line Sensor]() |  | 

### Printed Parts

Qty | Part Name | Image
--- | --- | ---
1 | [Line Sensor Holder](../printedparts/stl/LineSensorHolder.stl) |  | 

### Assembly Steps

1. Insert the two line sensor modules


## Left Drive Wheel

### Vitamins

Qty | Vitamin | Image
--- | --- | ---
1 | [28YBJ48 Stepper Motor]() |  | 
1 | [ULN2003 Driver Board]() |  | 

### Printed Parts

Qty | Part Name | Image
--- | --- | ---
1 | [Left Motor Clip](../printedparts/stl/LeftMotorClip.stl) |  | 
2 | [Pin Tack H7](../printedparts/stl/PinTackH7.stl) |  | 
1 | [Wheel](../printedparts/stl/Wheel.stl) |  | 

### Assembly Animation



### Assembly Steps

1. Clip the motor into place

2. Push the pins into the motor clip

3. Push the wheel onto the motor shaft, then add a rubber band or o-ring to the wheel for extra grip.  You can also add a retaining grub screw if necessary.

4. Slide the stepper driver into place and plug in the cable for the motor


## Right Drive Wheel

### Vitamins

Qty | Vitamin | Image
--- | --- | ---
1 | [28YBJ48 Stepper Motor]() |  | 
1 | [ULN2003 Driver Board]() |  | 

### Printed Parts

Qty | Part Name | Image
--- | --- | ---
2 | [Pin Tack H7](../printedparts/stl/PinTackH7.stl) |  | 
1 | [Right Motor Clip](../printedparts/stl/RightMotorClip.stl) |  | 
1 | [Wheel](../printedparts/stl/Wheel.stl) |  | 

### Assembly Animation



### Assembly Steps

1. Clip the motor into place

2. Push the pins into the motor clip

3. Push the wheel onto the motor shaft, then add a rubber band or o-ring to the wheel for extra grip.  You can also add a retaining grub screw if necessary.

4. Slide the stepper driver into place and plug in the cable for the motor


## Rear Caster

### Vitamins

Qty | Vitamin | Image
--- | --- | ---
1 | [16mm Marble]() |  | 

### Printed Parts

Qty | Part Name | Image
--- | --- | ---
1 | [Caster Housing](../printedparts/stl/CasterHousing.stl) |  | 

### Assembly Animation



### Assembly Steps

1. Insert the marble into the printed housing


## Final Assembly

### Vitamins

Qty | Vitamin | Image
--- | --- | ---
1 | [Arduino Pro Mini Pins on top, inc serial pins]() |  | 
4 | [AA Battery]() |  | 
1 | [Battery Pack]() |  | 
1 | [Hook and Loop Tape 40x10mm]() |  | 
2 | [JumperWire Female to Female 4pin 100mm]() |  | 
4 | [JumperWire Female to None 1pin 100mm]() |  | 
4 | [JumperWire Female to None 1pin 70mm]() |  | 
2 | [JumperWire None to None 1pin 100mm]() |  | 
3 | [JumperWire None to None 1pin 50mm]() |  | 
1 | [SPST6A Mini Toggle Switch]() |  | 
1 | [2 Pole 20A Terminal Block]() |  | 

### Printed Parts

Qty | Part Name | Image
--- | --- | ---
1 | [Base](../printedparts/stl/Base.stl) |  | 
1 | [Pin Tack H6.1](../printedparts/stl/PinTackH61.stl) |  | 
1 | [Pin Tack H7](../printedparts/stl/PinTackH7.stl) |  | 

### Sub-Assemblies

Qty | Name 
--- | --- 
1 | Line Sensor
1 | Left Drive Wheel
1 | Right Drive Wheel
1 | Rear Caster

### Assembly Steps

1. Plug the Pro Mini Clips into the base and then snap the Arduino Pro Mini into them

2. Pin the line sensor assembly to the underside

4. Plug the two wheels assemblies into the base

5. Connect the jumper wires between the motor drivers and the Arduino


6. Fix the power toggle switch into place

9. Align the caster assembly with the base, then insert a short pin to lock it to the base

11. Attach the battery pack with self-adhesive hook and loop tape

12. Wire in the terminal block to distribute power

13. Wire up power to the stepper drivers and Arduino.  Then connect the microswitches to the Arduino.


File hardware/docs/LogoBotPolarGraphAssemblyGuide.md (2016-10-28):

# LogoBot Polar Graph
# Assembly Guide

view

Re-uses most of the LogoBot vitamins and printed parts to make a basic polar graph drawing machine

## Bill of Materials

Make sure you have all of the following parts before you begin.

### Vitamins

Qty | Vitamin | Image
--- | --- | ---
1 | [Arduino Pro Mini Pins on top, inc serial pins]() |  | 
8 | [3mm LED]() |  | 
3 | [16mm Marble]() |  | 
1 | [9g Micro Servo]() |  | 
1 | [Fine Line Pen]() |  | 
1 | [Servo Horn]() |  | 
2 | [28YBJ48 Stepper Motor]() |  | 
2 | [ULN2003 Driver Board]() |  | 
4 | [No6 cs  wood screw x 20mm]() |  | 

### Printed Parts

Qty | Part Name | Image
--- | --- | ---
2 | [Capstan](../printedparts/stl/Capstan.stl) |  | 
1 | [Left Motor Clip](../printedparts/stl/LeftMotorClip.stl) |  | 
1 | [Base](../printedparts/stl/Base.stl) |  | 
3 | [Caster Housing](../printedparts/stl/CasterHousing.stl) |  | 
1 | [Pen Lift Holder](../printedparts/stl/PenLiftHolder.stl) |  | 
1 | [Pen Lift Slider](../printedparts/stl/PenLiftSlider.stl) |  | 
2 | [Pin Tack H9](../printedparts/stl/PinTackH9.stl) |  | 
1 | [Right Motor Clip](../printedparts/stl/RightMotorClip.stl) |  | 

**Plastic Required**

52.1cm3, 0.07KG,  approx: 0.85 GBP

# Assembly Instructions

## PenLift

### Vitamins

Qty | Vitamin | Image
--- | --- | ---
1 | [Fine Line Pen]() |  | 

### Printed Parts

Qty | Part Name | Image
--- | --- | ---
1 | [Pen Lift Holder](../printedparts/stl/PenLiftHolder.stl) |  | 
1 | [Pen Lift Slider](../printedparts/stl/PenLiftSlider.stl) |  | 

### Assembly Steps

1. Place the pen holder into the pen slider plate.  Ensure they move freely, the two parts should fall apart easily.  Lightly file or sand the pen holder part if they dont.  Fit an elastic band in the lower grooves and over the top of the mechanism so that it pulls the pen holder down in the slider mechanism.

2. Use a small elastic band to securely fasten the pen to the holder.  Make sure that the pen is held vertically and that the nib of the pen will be touching the ground when the slider is almost, but not quite, fully down.


## Rear Caster (x3)

### Vitamins

Qty | Vitamin | Image
--- | --- | ---
3 | [16mm Marble]() |  | 

### Printed Parts

Qty | Part Name | Image
--- | --- | ---
3 | [Caster Housing](../printedparts/stl/CasterHousing.stl) |  | 

### Assembly Animation



### Assembly Steps

1. Insert the marble into the printed housing


## Left Capstan

### Vitamins

Qty | Vitamin | Image
--- | --- | ---
1 | [28YBJ48 Stepper Motor]() |  | 
1 | [ULN2003 Driver Board]() |  | 

### Printed Parts

Qty | Part Name | Image
--- | --- | ---
1 | [Capstan](../printedparts/stl/Capstan.stl) |  | 
1 | [Left Motor Clip](../printedparts/stl/LeftMotorClip.stl) |  | 

### Assembly Steps

1. Clip the motor into place

2. Push the capstan onto the motor shaft.  You can also add a retaining grub screw if necessary.

3. Slide the stepper driver into place and plug in the cable for the motor


## Right Capstan

### Vitamins

Qty | Vitamin | Image
--- | --- | ---
1 | [28YBJ48 Stepper Motor]() |  | 
1 | [ULN2003 Driver Board]() |  | 

### Printed Parts

Qty | Part Name | Image
--- | --- | ---
1 | [Capstan](../printedparts/stl/Capstan.stl) |  | 
1 | [Right Motor Clip](../printedparts/stl/RightMotorClip.stl) |  | 

### Assembly Steps

1. Clip the motor into place

2. Push the capstan onto the motor shaft.  You can also add a retaining grub screw if necessary.

3. Slide the stepper driver into place and plug in the cable for the motor


## Gondola

### Vitamins

Qty | Vitamin | Image
--- | --- | ---
1 | [9g Micro Servo]() |  | 
1 | [Servo Horn]() |  | 

### Printed Parts

Qty | Part Name | Image
--- | --- | ---
1 | [Base](../printedparts/stl/Base.stl) |  | 
2 | [Pin Tack H9](../printedparts/stl/PinTackH9.stl) |  | 

### Sub-Assemblies

Qty | Name 
--- | --- 
1 | PenLift
3 | Rear Caster

### Assembly Steps

1. Attach the pen lift

2. Attach the three castors


## LogoBot Polar Graph

### Vitamins

Qty | Vitamin | Image
--- | --- | ---
1 | [Arduino Pro Mini Pins on top, inc serial pins]() |  | 
4 | [No6 cs  wood screw x 20mm]() |  | 

### Sub-Assemblies

Qty | Name 
--- | --- 
1 | Left Capstan
1 | Right Capstan
1 | Gondola

### Assembly Steps

1. Cut a piece of wood to 500mm long, at least 20mm x 20mm cross section

2. Screw the capstan assemblies to the wooden beam, the axles should be 440mm apart.

3. String up the gondola using fishing line

10. Fix the arduino to the center of the beam - 200mm jumper wires should just reach from the motor drivers

20. Screw, tape or otherwise fix the polargraph onto the top of a suitable drawing surface - flipchart stands work well.


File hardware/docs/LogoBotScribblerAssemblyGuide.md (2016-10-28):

# LogoBot Scribbler
# Assembly Guide

view

## Bill of Materials

Make sure you have all of the following parts before you begin.

### Vitamins

Qty | Vitamin | Image
--- | --- | ---
1 | [Arduino Pro Mini Pins on top, inc serial pins]() |  | 
4 | [AA Battery]() |  | 
1 | [Battery Pack]() |  | 
1 | [Hook and Loop Tape 40x10mm]() |  | 
2 | [JumperWire Female to Female 4pin 100mm]() |  | 
6 | [JumperWire Female to None 1pin 100mm]() |  | 
4 | [JumperWire Female to None 1pin 70mm]() |  | 
4 | [JumperWire None to None 1pin 100mm]() |  | 
3 | [JumperWire None to None 1pin 50mm]() |  | 
8 | [3mm LED]() |  | 
1 | [16mm Marble]() |  | 
1 | [9g Micro Servo]() |  | 
4 | [MicroSwitch]() |  | 
1 | [SPST6A Mini Toggle Switch]() |  | 
1 | [Fine Line Pen]() |  | 
1 | [Servo Horn]() |  | 
2 | [28YBJ48 Stepper Motor]() |  | 
1 | [2 Pole 20A Terminal Block]() |  | 
2 | [ULN2003 Driver Board]() |  | 

### Printed Parts

Qty | Part Name | Image
--- | --- | ---
1 | [Basic Shell](../printedparts/stl/BasicShell.stl) |  | 
2 | [BumperStabiliser](../printedparts/stl/BumperStabiliser.stl) |  | 
2 | [Bumper](../printedparts/stl/Bumper.stl) |  | 
1 | [Left Motor Clip](../printedparts/stl/LeftMotorClip.stl) |  | 
1 | [Base](../printedparts/stl/Base.stl) |  | 
1 | [Caster Housing](../printedparts/stl/CasterHousing.stl) |  | 
1 | [Pen Lift Holder](../printedparts/stl/PenLiftHolder.stl) |  | 
1 | [Pen Lift Slider](../printedparts/stl/PenLiftSlider.stl) |  | 
4 | [Pin Tack H14.1](../printedparts/stl/PinTackH141.stl) |  | 
1 | [Pin Tack H6.1](../printedparts/stl/PinTackH61.stl) |  | 
4 | [Pin Tack H7](../printedparts/stl/PinTackH7.stl) |  | 
2 | [Pin Tack H9](../printedparts/stl/PinTackH9.stl) |  | 
2 | [Pro Mini Clip](../printedparts/stl/ProMiniClip.stl) |  | 
1 | [Right Motor Clip](../printedparts/stl/RightMotorClip.stl) |  | 
2 | [Wheel](../printedparts/stl/Wheel.stl) |  | 

**Plastic Required**

150.3cm3, 0.19KG,  approx: 2.44 GBP

# Assembly Instructions

## Bumpers (x2)

### Vitamins

Qty | Vitamin | Image
--- | --- | ---
4 | [MicroSwitch]() |  | 

### Printed Parts

Qty | Part Name | Image
--- | --- | ---
2 | [Bumper](../printedparts/stl/Bumper.stl) |  | 

### Assembly Animation



### Assembly Steps

1. Place the Microswitches into the holders.  Make sure to get them the right way round so the bumper hits the metal lever.  Repeat for the second bumper.


## Left Drive Wheel

### Vitamins

Qty | Vitamin | Image
--- | --- | ---
1 | [28YBJ48 Stepper Motor]() |  | 
1 | [ULN2003 Driver Board]() |  | 

### Printed Parts

Qty | Part Name | Image
--- | --- | ---
1 | [Left Motor Clip](../printedparts/stl/LeftMotorClip.stl) |  | 
2 | [Pin Tack H7](../printedparts/stl/PinTackH7.stl) |  | 
1 | [Wheel](../printedparts/stl/Wheel.stl) |  | 

### Assembly Animation



### Assembly Steps

1. Clip the motor into place

2. Push the pins into the motor clip

3. Push the wheel onto the motor shaft, then add a rubber band or o-ring to the wheel for extra grip.  You can also add a retaining grub screw if necessary.

4. Slide the stepper driver into place and plug in the cable for the motor


## Right Drive Wheel

### Vitamins

Qty | Vitamin | Image
--- | --- | ---
1 | [28YBJ48 Stepper Motor]() |  | 
1 | [ULN2003 Driver Board]() |  | 

### Printed Parts

Qty | Part Name | Image
--- | --- | ---
2 | [Pin Tack H7](../printedparts/stl/PinTackH7.stl) |  | 
1 | [Right Motor Clip](../printedparts/stl/RightMotorClip.stl) |  | 
1 | [Wheel](../printedparts/stl/Wheel.stl) |  | 

### Assembly Animation



### Assembly Steps

1. Clip the motor into place

2. Push the pins into the motor clip

3. Push the wheel onto the motor shaft, then add a rubber band or o-ring to the wheel for extra grip.  You can also add a retaining grub screw if necessary.

4. Slide the stepper driver into place and plug in the cable for the motor


## Rear Caster

### Vitamins

Qty | Vitamin | Image
--- | --- | ---
1 | [16mm Marble]() |  | 

### Printed Parts

Qty | Part Name | Image
--- | --- | ---
1 | [Caster Housing](../printedparts/stl/CasterHousing.stl) |  | 

### Assembly Animation



### Assembly Steps

1. Insert the marble into the printed housing


## PenLift

### Vitamins

Qty | Vitamin | Image
--- | --- | ---
1 | [Fine Line Pen]() |  | 

### Printed Parts

Qty | Part Name | Image
--- | --- | ---
1 | [Pen Lift Holder](../printedparts/stl/PenLiftHolder.stl) |  | 
1 | [Pen Lift Slider](../printedparts/stl/PenLiftSlider.stl) |  | 

### Assembly Steps

1. Place the pen holder into the pen slider plate.  Ensure they move freely, the two parts should fall apart easily.  Lightly file or sand the pen holder part if they dont.  Fit an elastic band in the lower grooves and over the top of the mechanism so that it pulls the pen holder down in the slider mechanism.

2. Use a small elastic band to securely fasten the pen to the holder.  Make sure that the pen is held vertically and that the nib of the pen will be touching the ground when the slider is almost, but not quite, fully down.


## Final Assembly

### Vitamins

Qty | Vitamin | Image
--- | --- | ---
1 | [Arduino Pro Mini Pins on top, inc serial pins]() |  | 
4 | [AA Battery]() |  | 
1 | [Battery Pack]() |  | 
1 | [Hook and Loop Tape 40x10mm]() |  | 
2 | [JumperWire Female to Female 4pin 100mm]() |  | 
6 | [JumperWire Female to None 1pin 100mm]() |  | 
4 | [JumperWire Female to None 1pin 70mm]() |  | 
4 | [JumperWire None to None 1pin 100mm]() |  | 
3 | [JumperWire None to None 1pin 50mm]() |  | 
1 | [9g Micro Servo]() |  | 
1 | [SPST6A Mini Toggle Switch]() |  | 
1 | [Servo Horn]() |  | 
1 | [2 Pole 20A Terminal Block]() |  | 

### Printed Parts

Qty | Part Name | Image
--- | --- | ---
2 | [BumperStabiliser](../printedparts/stl/BumperStabiliser.stl) |  | 
1 | [Base](../printedparts/stl/Base.stl) |  | 
4 | [Pin Tack H14.1](../printedparts/stl/PinTackH141.stl) |  | 
1 | [Pin Tack H6.1](../printedparts/stl/PinTackH61.stl) |  | 
2 | [Pin Tack H9](../printedparts/stl/PinTackH9.stl) |  | 
2 | [Pro Mini Clip](../printedparts/stl/ProMiniClip.stl) |  | 

### Sub-Assemblies

Qty | Name 
--- | --- 
2 | Bumpers
1 | Left Drive Wheel
1 | Right Drive Wheel
1 | Rear Caster
1 | PenLift
1 | Shell

### Assembly Animation



### Assembly Steps

1. Plug the Pro Mini Clips into the base and then snap the Arduino Pro Mini into them

2. Connect the two bumper assemblies using four of the push pins with flat heads


4. Plug the two wheels assemblies into the base

5. Connect the jumper wires between the motor drivers and the Arduino


6. Fix the power toggle switch into place

9. Align the caster assembly with the base, then insert a short pin to lock it to the base

10. Fit the pen lift assembly using two of the pins and zip tie the servo under the base.

11. Attach the battery pack with self-adhesive hook and loop tape

12. Wire in the terminal block to distribute power

13. Wire up power to the stepper drivers and Arduino.  Then connect the microswitches to the Arduino. 
            Refer to the following wiring for Arduino pin connections: 
            Arduino Wiring Diagram

14. Push the shell down onto the base and twist to lock into place


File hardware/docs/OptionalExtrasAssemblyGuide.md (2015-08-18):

# OptionalExtras
# Assembly Guide

view

## Bill of Materials

Make sure you have all of the following parts before you begin.

### Printed Parts

Qty | Part Name | Image
--- | --- | ---
1 | [Lego Lid](../printedparts/stl/LegoLid.stl) |  | 
1 | [Simple Base](../printedparts/stl/SimpleBase.stl) |  | 
1 | [Voronoi Shell Type1](../printedparts/stl/VoronoiShellType1.stl) |  | 
1 | [Voronoi Shell Type2](../printedparts/stl/VoronoiShellType2.stl) |  | 

**Plastic Required**

94.6cm3, 0.12KG,  approx: 1.54 GBP

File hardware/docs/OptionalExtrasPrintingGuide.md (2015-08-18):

# OptionalExtras
# Printing Guide

### Lego Lid

Metric | Value 
--- | --- 
Quantity | 1
STL | [Lego Lid](../printedparts/stl/LegoLid.stl)
Plastic (Kg) | 0.02
Plastic (cm3) | 13.2
Approx Plastic Cost | 0.25 GBP



### Simple Base

Metric | Value 
--- | --- 
Quantity | 1
STL | [Simple Base](../printedparts/stl/SimpleBase.stl)
Plastic (Kg) | 0.01
Plastic (cm3) | 10.7
Approx Plastic Cost | 0.2 GBP



**Notes**

 * The base requires a well calibrated printer to avoid adhesion issues.  You may also need to ream the holes to 7mm, depending on your print tolerances.

### Voronoi Shell Type1

Metric | Value 
--- | --- 
Quantity | 1
STL | [Voronoi Shell Type1](../printedparts/stl/VoronoiShellType1.stl)
Plastic (Kg) | 0.04
Plastic (cm3) | 29.5
Approx Plastic Cost | 0.55 GBP



### Voronoi Shell Type2

Metric | Value 
--- | --- 
Quantity | 1
STL | [Voronoi Shell Type2](../printedparts/stl/VoronoiShellType2.stl)
Plastic (Kg) | 0.05
Plastic (cm3) | 41.2
Approx Plastic Cost | 0.77 GBP



## Summary

### Statistics

Metric | Value 
--- | --- 
Total Parts | 4
Total Plastic (Kg) | 0.12KG
Total Plastic (cm3) | 94.6cm3
Approx Plastic Cost | 1.77 GBP

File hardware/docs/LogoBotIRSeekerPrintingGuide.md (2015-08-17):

# LogoBot IR Seeker
# Printing Guide

### Basic Shell

Metric | Value 
--- | --- 
Quantity | 1
STL | [Basic Shell](../printedparts/stl/BasicShell.stl)
Plastic (Kg) | 0.08
Plastic (cm3) | 66.7
Approx Plastic Cost | 1.25 GBP



**Notes**

 * The shell has a maximum overhang of 60 degrees and should print without support on most printers

### BumperStabiliser

Metric | Value 
--- | --- 
Quantity | 2
STL | [BumperStabiliser](../printedparts/stl/BumperStabiliser.stl)
Plastic (Kg) | 0.0
Plastic (cm3) | 2.2
Approx Plastic Cost | 0.04 GBP



### Bumper

Metric | Value 
--- | --- 
Quantity | 2
STL | [Bumper](../printedparts/stl/Bumper.stl)
Plastic (Kg) | 0.03
Plastic (cm3) | 25.2
Approx Plastic Cost | 0.47 GBP



### IR Servo Bracket

Metric | Value 
--- | --- 
Quantity | 1
STL | [IR Servo Bracket](../printedparts/stl/IRServoBracket.stl)
Plastic (Kg) | 0.01
Plastic (cm3) | 4.9
Approx Plastic Cost | 0.09 GBP



### Left Motor Clip

Metric | Value 
--- | --- 
Quantity | 1
STL | [Left Motor Clip](../printedparts/stl/LeftMotorClip.stl)
Plastic (Kg) | 0.01
Plastic (cm3) | 5.1
Approx Plastic Cost | 0.1 GBP



**Notes**

 * MotorClips need re-orienting before printing so that the base of the motor clip sits on the bed

### LidIR

Metric | Value 
--- | --- 
Quantity | 1
STL | [LidIR](../printedparts/stl/LidIR.stl)
Plastic (Kg) | 0.02
Plastic (cm3) | 14.0
Approx Plastic Cost | 0.26 GBP



**Notes**

 * Includes built-in support material which should easily break out after printing

### Base

Metric | Value 
--- | --- 
Quantity | 1
STL | [Base](../printedparts/stl/Base.stl)
Plastic (Kg) | 0.03
Plastic (cm3) | 21.2
Approx Plastic Cost | 0.4 GBP



**Notes**

 * The base requires a well calibrated printer to avoid adhesion issues.  You may also need to ream the holes to 7mm, depending on your print tolerances.

### Caster Housing

Metric | Value 
--- | --- 
Quantity | 1
STL | [Caster Housing](../printedparts/stl/CasterHousing.stl)
Plastic (Kg) | 0.0
Plastic (cm3) | 1.4
Approx Plastic Cost | 0.03 GBP



**Notes**

 * Orient to print upside down for best results.  No support required.  A brim may help with bed adhesion and would not need to removed after printing.  Ream the pin hole to 7mm if necessary.

### Pin Tack H14.1

Metric | Value 
--- | --- 
Quantity | 4
STL | [Pin Tack H14.1](../printedparts/stl/PinTackH141.stl)
Plastic (Kg) | 0.0
Plastic (cm3) | 1.6
Approx Plastic Cost | 0.03 GBP



**Notes**

 * Orient to print on the flat side, no brim.  You may need to sand the flat sides depending on the tolerances of your printer.

### Pin Tack H6.1

Metric | Value 
--- | --- 
Quantity | 1
STL | [Pin Tack H6.1](../printedparts/stl/PinTackH61.stl)
Plastic (Kg) | 0.0
Plastic (cm3) | 0.3
Approx Plastic Cost | 0.01 GBP



**Notes**

 * Orient to print on the flat side, no brim.  You may need to sand the flat sides depending on the tolerances of your printer.

### Pin Tack H6.5

Metric | Value 
--- | --- 
Quantity | 2
STL | [Pin Tack H6.5](../printedparts/stl/PinTackH65.stl)
Plastic (Kg) | 0.0
Plastic (cm3) | 0.6
Approx Plastic Cost | 0.01 GBP



**Notes**

 * Orient to print on the flat side, no brim.  You may need to sand the flat sides depending on the tolerances of your printer.

### Pin Tack H7

Metric | Value 
--- | --- 
Quantity | 4
STL | [Pin Tack H7](../printedparts/stl/PinTackH7.stl)
Plastic (Kg) | 0.0
Plastic (cm3) | 1.2
Approx Plastic Cost | 0.02 GBP



**Notes**

 * Orient to print on the flat side, no brim.  You may need to sand the flat sides depending on the tolerances of your printer.

### Pro Mini Clip

Metric | Value 
--- | --- 
Quantity | 2
STL | [Pro Mini Clip](../printedparts/stl/ProMiniClip.stl)
Plastic (Kg) | 0.0
Plastic (cm3) | 0.6
Approx Plastic Cost | 0.01 GBP



### Right Motor Clip

Metric | Value 
--- | --- 
Quantity | 1
STL | [Right Motor Clip](../printedparts/stl/RightMotorClip.stl)
Plastic (Kg) | 0.01
Plastic (cm3) | 5.1
Approx Plastic Cost | 0.1 GBP



**Notes**

 * MotorClips need re-orienting before printing so that the base of the motor clip sits on the bed

### Wheel

Metric | Value 
--- | --- 
Quantity | 2
STL | [Wheel](../printedparts/stl/Wheel.stl)
Plastic (Kg) | 0.01
Plastic (cm3) | 9.0
Approx Plastic Cost | 0.17 GBP



## Summary

### Statistics

Metric | Value 
--- | --- 
Total Parts | 26
Total Plastic (Kg) | 0.2KG
Total Plastic (cm3) | 159.1cm3
Approx Plastic Cost | 2.98 GBP

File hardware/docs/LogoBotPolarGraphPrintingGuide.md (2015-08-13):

# LogoBot Polar Graph
# Printing Guide

### Capstan

Metric | Value 
--- | --- 
Quantity | 2
STL | [Capstan](../printedparts/stl/Capstan.stl)
Plastic (Kg) | 0.01
Plastic (cm3) | 5.8
Approx Plastic Cost | 0.11 GBP



### Left Motor Clip

Metric | Value 
--- | --- 
Quantity | 1
STL | [Left Motor Clip](../printedparts/stl/LeftMotorClip.stl)
Plastic (Kg) | 0.01
Plastic (cm3) | 5.1
Approx Plastic Cost | 0.1 GBP



**Notes**

 * MotorClips need re-orienting before printing so that the base of the motor clip sits on the bed

### Base

Metric | Value 
--- | --- 
Quantity | 1
STL | [Base](../printedparts/stl/Base.stl)
Plastic (Kg) | 0.03
Plastic (cm3) | 21.2
Approx Plastic Cost | 0.4 GBP



**Notes**

 * The base requires a well calibrated printer to avoid adhesion issues.  You may also need to ream the holes to 7mm, depending on your print tolerances.

### Caster Housing

Metric | Value 
--- | --- 
Quantity | 3
STL | [Caster Housing](../printedparts/stl/CasterHousing.stl)
Plastic (Kg) | 0.01
Plastic (cm3) | 4.5
Approx Plastic Cost | 0.08 GBP



**Notes**

 * Orient to print upside down for best results.  No support required.  A brim may help with bed adhesion and would not need to removed after printing.  Ream the pin hole to 7mm if necessary.

### Pen Lift Holder

Metric | Value 
--- | --- 
Quantity | 1
STL | [Pen Lift Holder](../printedparts/stl/PenLiftHolder.stl)
Plastic (Kg) | 0.01
Plastic (cm3) | 5.7
Approx Plastic Cost | 0.11 GBP



**Notes**

 * You may need to ream the pin holes to 7mm, depending on your print tolerances

### Pen Lift Slider

Metric | Value 
--- | --- 
Quantity | 1
STL | [Pen Lift Slider](../printedparts/stl/PenLiftSlider.stl)
Plastic (Kg) | 0.01
Plastic (cm3) | 4.1
Approx Plastic Cost | 0.08 GBP



**Notes**

 * Slider will probably require some sanding to get a smooth fit into the holder.  A bit of silicon spray lubricant may also help.

### Pin Tack H9

Metric | Value 
--- | --- 
Quantity | 2
STL | [Pin Tack H9](../printedparts/stl/PinTackH9.stl)
Plastic (Kg) | 0.0
Plastic (cm3) | 0.6
Approx Plastic Cost | 0.01 GBP



**Notes**

 * Orient to print on the flat side, no brim.  You may need to sand the flat sides depending on the tolerances of your printer.

### Right Motor Clip

Metric | Value 
--- | --- 
Quantity | 1
STL | [Right Motor Clip](../printedparts/stl/RightMotorClip.stl)
Plastic (Kg) | 0.01
Plastic (cm3) | 5.1
Approx Plastic Cost | 0.1 GBP



**Notes**

 * MotorClips need re-orienting before printing so that the base of the motor clip sits on the bed

## Summary

### Statistics

Metric | Value 
--- | --- 
Total Parts | 12
Total Plastic (Kg) | 0.07KG
Total Plastic (cm3) | 52.1cm3
Approx Plastic Cost | 0.98 GBP

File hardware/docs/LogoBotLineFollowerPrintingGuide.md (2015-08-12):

# LogoBot Line Follower
# Printing Guide

### Left Motor Clip

Metric | Value 
--- | --- 
Quantity | 1
STL | [Left Motor Clip](../printedparts/stl/LeftMotorClip.stl)
Plastic (Kg) | 0.01
Plastic (cm3) | 5.0
Approx Plastic Cost | 0.09 GBP



**Notes**

 * MotorClips need re-orienting before printing so that the base of the motor clip sits on the bed

### Line Sensor Holder

Metric | Value 
--- | --- 
Quantity | 1
STL | [Line Sensor Holder](../printedparts/stl/LineSensorHolder.stl)
Plastic (Kg) | 0.0
Plastic (cm3) | 2.5
Approx Plastic Cost | 0.05 GBP



**Notes**

 * No support required, pin hole may need to be reamed to 7mm

### Base

Metric | Value 
--- | --- 
Quantity | 1
STL | [Base](../printedparts/stl/Base.stl)
Plastic (Kg) | 0.03
Plastic (cm3) | 21.2
Approx Plastic Cost | 0.4 GBP



**Notes**

 * The base requires a well calibrated printer to avoid adhesion issues.  You may also need to ream the holes to 7mm, depending on your print tolerances.

### Caster Housing

Metric | Value 
--- | --- 
Quantity | 1
STL | [Caster Housing](../printedparts/stl/CasterHousing.stl)
Plastic (Kg) | 0.0
Plastic (cm3) | 1.5
Approx Plastic Cost | 0.03 GBP



**Notes**

 * Orient to print upside down for best results.  No support required.  A brim may help with bed adhesion and would not need to removed after printing.  Ream the pin hole to 7mm if necessary.

### Pin Tack H6.1

Metric | Value 
--- | --- 
Quantity | 1
STL | [Pin Tack H6.1](../printedparts/stl/PinTackH61.stl)
Plastic (Kg) | 0.0
Plastic (cm3) | 0.3
Approx Plastic Cost | 0.01 GBP



**Notes**

 * Orient to print on the flat side, no brim.  You may need to sand the flat sides depending on the tolerances of your printer.

### Pin Tack H7

Metric | Value 
--- | --- 
Quantity | 5
STL | [Pin Tack H7](../printedparts/stl/PinTackH7.stl)
Plastic (Kg) | 0.0
Plastic (cm3) | 1.5
Approx Plastic Cost | 0.03 GBP



**Notes**

 * Orient to print on the flat side, no brim.  You may need to sand the flat sides depending on the tolerances of your printer.

### Right Motor Clip

Metric | Value 
--- | --- 
Quantity | 1
STL | [Right Motor Clip](../printedparts/stl/RightMotorClip.stl)
Plastic (Kg) | 0.01
Plastic (cm3) | 5.0
Approx Plastic Cost | 0.09 GBP



**Notes**

 * MotorClips need re-orienting before printing so that the base of the motor clip sits on the bed

### Wheel

Metric | Value 
--- | --- 
Quantity | 2
STL | [Wheel](../printedparts/stl/Wheel.stl)
Plastic (Kg) | 0.01
Plastic (cm3) | 9.0
Approx Plastic Cost | 0.17 GBP



## Summary

### Statistics

Metric | Value 
--- | --- 
Total Parts | 13
Total Plastic (Kg) | 0.06KG
Total Plastic (cm3) | 46.0cm3
Approx Plastic Cost | 0.86 GBP

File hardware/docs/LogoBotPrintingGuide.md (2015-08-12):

# LogoBot
# Printing Guide

### Basic Shell

Metric | Value 
--- | --- 
Quantity | 1
STL | [Basic Shell](../printedparts/stl/BasicShell.stl)
Plastic (Kg) | 0.08
Plastic (cm3) | 66.7
Approx Plastic Cost | 1.25 GBP



**Notes**

 * The shell has a maximum overhang of 60 degrees and should print without support on most printers

### BumperStabiliser

Metric | Value 
--- | --- 
Quantity | 2
STL | [BumperStabiliser](../printedparts/stl/BumperStabiliser.stl)
Plastic (Kg) | 0.0
Plastic (cm3) | 2.2
Approx Plastic Cost | 0.04 GBP



### Bumper

Metric | Value 
--- | --- 
Quantity | 2
STL | [Bumper](../printedparts/stl/Bumper.stl)
Plastic (Kg) | 0.03
Plastic (cm3) | 25.8
Approx Plastic Cost | 0.48 GBP



### Left Motor Clip

Metric | Value 
--- | --- 
Quantity | 1
STL | [Left Motor Clip](../printedparts/stl/LeftMotorClip.stl)
Plastic (Kg) | 0.01
Plastic (cm3) | 4.9
Approx Plastic Cost | 0.09 GBP



**Notes**

 * MotorClips need re-orienting before printing so that the base of the motor clip sits on the bed

### Lid

Metric | Value 
--- | --- 
Quantity | 1
STL | [Lid](../printedparts/stl/Lid.stl)
Plastic (Kg) | 0.02
Plastic (cm3) | 13.9
Approx Plastic Cost | 0.26 GBP



**Notes**

 * Includes built-in support material which should easily break out after printing

### Base

Metric | Value 
--- | --- 
Quantity | 1
STL | [Base](../printedparts/stl/Base.stl)
Plastic (Kg) | 0.03
Plastic (cm3) | 21.2
Approx Plastic Cost | 0.4 GBP



**Notes**

 * The base requires a well calibrated printer to avoid adhesion issues.  You may also need to ream the holes to 7mm, depending on your print tolerances.

### Caster Housing

Metric | Value 
--- | --- 
Quantity | 1
STL | [Caster Housing](../printedparts/stl/CasterHousing.stl)
Plastic (Kg) | 0.0
Plastic (cm3) | 1.5
Approx Plastic Cost | 0.03 GBP



**Notes**

 * Orient to print upside down for best results.  No support required.  A brim may help with bed adhesion and would not need to removed after printing.  Ream the pin hole to 7mm if necessary.

### Pin Tack H14.1

Metric | Value 
--- | --- 
Quantity | 4
STL | [Pin Tack H14.1](../printedparts/stl/PinTackH141.stl)
Plastic (Kg) | 0.0
Plastic (cm3) | 1.6
Approx Plastic Cost | 0.03 GBP



**Notes**

 * Orient to print on the flat side, no brim.  You may need to sand the flat sides depending on the tolerances of your printer.

### Pin Tack H6.1

Metric | Value 
--- | --- 
Quantity | 1
STL | [Pin Tack H6.1](../printedparts/stl/PinTackH61.stl)
Plastic (Kg) | 0.0
Plastic (cm3) | 0.3
Approx Plastic Cost | 0.01 GBP



**Notes**

 * Orient to print on the flat side, no brim.  You may need to sand the flat sides depending on the tolerances of your printer.

### Pin Tack H7

Metric | Value 
--- | --- 
Quantity | 4
STL | [Pin Tack H7](../printedparts/stl/PinTackH7.stl)
Plastic (Kg) | 0.0
Plastic (cm3) | 1.2
Approx Plastic Cost | 0.02 GBP



**Notes**

 * Orient to print on the flat side, no brim.  You may need to sand the flat sides depending on the tolerances of your printer.

### Pro Mini Clip

Metric | Value 
--- | --- 
Quantity | 2
STL | [Pro Mini Clip](../printedparts/stl/ProMiniClip.stl)
Plastic (Kg) | 0.0
Plastic (cm3) | 0.6
Approx Plastic Cost | 0.01 GBP



### Right Motor Clip

Metric | Value 
--- | --- 
Quantity | 1
STL | [Right Motor Clip](../printedparts/stl/RightMotorClip.stl)
Plastic (Kg) | 0.01
Plastic (cm3) | 4.9
Approx Plastic Cost | 0.09 GBP



**Notes**

 * MotorClips need re-orienting before printing so that the base of the motor clip sits on the bed

### Wheel

Metric | Value 
--- | --- 
Quantity | 2
STL | [Wheel](../printedparts/stl/Wheel.stl)
Plastic (Kg) | 0.01
Plastic (cm3) | 9.0
Approx Plastic Cost | 0.17 GBP



## Summary

### Statistics

Metric | Value 
--- | --- 
Total Parts | 23
Total Plastic (Kg) | 0.19KG
Total Plastic (cm3) | 153.8cm3
Approx Plastic Cost | 2.88 GBP

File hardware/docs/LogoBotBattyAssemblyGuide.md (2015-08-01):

# LogoBot Batty
# Assembly Guide

view

## Bill of Materials

Make sure you have all of the following parts before you begin.

### Vitamins

Qty | Vitamin | Image
--- | --- | ---
1 | [Breadboard 170]() |  | 
2 | [JumperWire Female to Male 4pin 100mm]() |  | 
1 | [16mm Marble]() |  | 

### Printed Parts

Qty | Part Name | Image
--- | --- | ---
1 | [Basic Shell](../printedparts/stl/BasicShell.stl) |  | 
2 | [Bumper](../printedparts/stl/Bumper.stl) |  | 
1 | [Lid](../printedparts/stl/Lid.stl) |  | 
1 | [Base](../printedparts/stl/Base.stl) |  | 
1 | [Caster Housing](../printedparts/stl/CasterHousing.stl) |  | 
2 | [Wheel](../printedparts/stl/Wheel.stl) |  | 
4 | [Pintack H14.1 BH2](../printedparts/stl/PintackH141BH2.stl) |  | 
1 | [Pintack H6.1 BH2](../printedparts/stl/PintackH61BH2.stl) |  | 

## Brain

### Vitamins

Qty | Vitamin | Image
--- | --- | ---
1 | [Breadboard 170]() |  | 

### Assembly Steps

1. Push the Arduino onto the breadboard - make sure you position it correctly,                  as it's a tight fit with the Robot base!


## Bumpers (x2)

### Printed Parts

Qty | Part Name | Image
--- | --- | ---
2 | [Bumper](../printedparts/stl/Bumper.stl) |  | 

### Assembly Steps

1. Place the Microswitches into the holders.  Make sure to get them the right way round so the bumper hits the metal lever.  Repeat for the second bumper.


## Drive Wheel (x2)

### Printed Parts

Qty | Part Name | Image
--- | --- | ---
2 | [Wheel](../printedparts/stl/Wheel.stl) |  | 

### Assembly Steps

1. Push the wheel onto the motor shaft **Optional:** add a rubber band to the wheel for extra grip.


## Rear Caster

### Vitamins

Qty | Vitamin | Image
--- | --- | ---
1 | [16mm Marble]() |  | 

### Printed Parts

Qty | Part Name | Image
--- | --- | ---
1 | [Caster Housing](../printedparts/stl/CasterHousing.stl) |  | 

### Assembly Steps

1. Insert the marble into the printed housing


## Shell

### Printed Parts

Qty | Part Name | Image
--- | --- | ---
1 | [Basic Shell](../printedparts/stl/BasicShell.stl) |  | 
1 | [Lid](../printedparts/stl/Lid.stl) |  | 

### Assembly Steps

1. Clip the lid onto the top of the shell


## Final Assembly

### Vitamins

Qty | Vitamin | Image
--- | --- | ---
2 | [JumperWire Female to Male 4pin 100mm]() |  | 

### Printed Parts

Qty | Part Name | Image
--- | --- | ---
1 | [Base](../printedparts/stl/Base.stl) |  | 
4 | [Pintack H14.1 BH2](../printedparts/stl/PintackH141BH2.stl) |  | 
1 | [Pintack H6.1 BH2](../printedparts/stl/PintackH61BH2.stl) |  | 

### Sub-Assemblies

Qty | Name 
--- | --- 
1 | Brain
2 | Bumpers
2 | Drive Wheel
1 | Rear Caster
1 | Shell

### Assembly Steps

1. Connect the breadboard assembly to the underside of the base

2. Connect the two bumper assemblies using four of the push pins with flat heads

3. Push the two motor drivers onto the mounting posts

4. Clip the two wheels assemblies onto the base and                    connect the motor leads to the the motor drivers

5. Connect the jumper wires between the motor drivers and the Arduino


6. Clip in the battery pack

7. Clip the power switch into place

8. Clip the LED into place

9. Clip the piezo sounder into place

10. Align the caster assembly with the base

11. Insert a short pin to lock the caster assembly to the base
12. Push the shell down onto the base and twist to lock into place


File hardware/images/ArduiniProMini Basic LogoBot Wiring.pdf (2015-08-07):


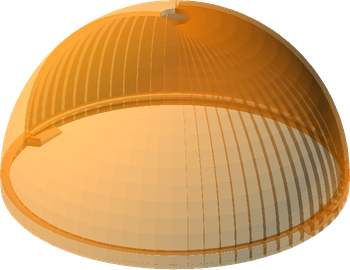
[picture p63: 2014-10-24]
hardware/printedparts/images/BasicShell_STL.png

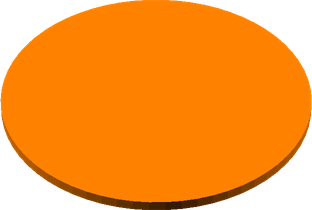
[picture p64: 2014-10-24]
hardware/printedparts/images/Wheel_STL.png

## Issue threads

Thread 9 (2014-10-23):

BatteryPack Clip

Axford, 2014-10-23:
@theorbtwo - your todo list for next week, please refine in sep branch and submit pull request by next Wed

To Do:
* Create a simple STL model that will hold the BatteryPack vitamin in place

Notes:
* Create the STL model in the sandbox for now, we'll merge it into the LogoBotBase_STL file during the wk3 session
* Would be great if you could bring along a print of the clip so we can all test/play with it next Wed

Axford, 2015-08-04:
Closing - collectively decided that velcro is the way to go! :)

Closed 2015-08-04.

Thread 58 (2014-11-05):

Pen vitamin

Axford, 2014-11-05:
Create a pen vitamin for the scribbler variant.

Axford, 2015-08-04:
done - Rob implemented Pen vitamin - based on a Uni Pin Fine Line 0.1mm (10mm diameter)

Part of the scribbler variant

Closed 2015-08-04.

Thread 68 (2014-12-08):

Enlarge shell opening, add Lid printed part

Axford, 2014-12-08:
Enlarge shell opening to ensure maximal print angle is <= 60 degrees - this should be stored in a new global parameter.

Create a new Lid printed part, and incorporate into the main LogoBot assembly as a final step.  An appropriate joint between the lid and shell needs to be defined, such that is is printable without support on the shell and requires minimal additional plastic within the lid part.

Axford, 2015-07-31:
done

Closed 2015-07-31.

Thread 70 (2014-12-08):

Make motor clips separate printed parts

Axford, 2014-12-08:
Split out the motor clips as separate printed parts.  Requirements as per recent discussions:

* Use pin system to mate to base plate
* Stronger clips, so the motor doesn't pop out and so they don't break (laminations should be aligned to front face of motor for strength)
* Add retaining wall with locating notch to stop motor sliding around and to stop it rotating within the clips.
* Incorporate holder for motor driver board, using spring clips with plenty of tolerance (to allow for changes in pcb dimensions as well as printer tolerance)

To consider:
* Cable management (e.g. cable tie fixing points or cable clips)

Axford, 2015-07-31:
done - can't rem which commit, but it was a while back

Closed 2015-07-31.

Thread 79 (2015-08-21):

Fix ProMiniClip

Axford, 2015-08-21:
Not enough flex/clearance in pin to reliably fit the pro mini clip to the base plate.  Probably needs a redesign.

Axford, 2015-08-22:
Latest version seems to work better (with the slimmer pin joint)...  needs further testing to be sure, but fingers crossed

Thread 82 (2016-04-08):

Link to stepper motor in Source Guide says this product is no longer available

q2dg, 2016-04-08:
I've found this other source (http://www.amazon.com/USPRO-Stepper-28BYJ-48-4-Phase-ULN2003/dp/B00JB22IQC) but maybe it would be a good idea offering some alternatives.
Thanks

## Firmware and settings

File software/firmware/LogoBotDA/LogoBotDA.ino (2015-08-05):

#include <DifferentialStepper.h>
#include <Logo.h>
//#include <LogoCommandQueue.h>
#include <Servo.h>

// Maths stuff
#define DEGTORAD  PI/180.0
#define RADTODEG  180.0/PI

// Pin definitions
// Left motor driver
#define motorLPin1  2     // IN1 on the ULN2003 driver 1
#define motorLPin2  3     // IN2 on the ULN2003 driver 1
#define motorLPin3  4     // IN3 on the ULN2003 driver 1
#define motorLPin4  5     // IN4 on the ULN2003 driver 1

// Right motor driver
#define motorRPin1  6     // IN1 on the ULN2003 driver 1
#define motorRPin2  7     // IN2 on the ULN2003 driver 1
#define motorRPin3  8     // IN3 on the ULN2003 driver 1
#define motorRPin4  9     // IN4 on the ULN2003 driver 1

// Piezo buzzer
#define buzzer      10

// Microswitches
#define switchFL    A0
#define switchFR    A1
#define switchBL    A2
#define switchBR    A3

// LED
#define InternalLED         13
#define LEDRED      11
#define LEDGREEN    12
#define LEDBLUE     13

// Servo for Pen Lift (Note same as LED for now)
#define SERVO       11

// Initialize with pin sequence IN1-IN3-IN2-IN4 for using the AccelStepper with 28BYJ-48
//AccelStepper stepperL(AccelStepper::HALF4WIRE, motorLPin1, motorLPin3, motorLPin2, motorLPin4);
//AccelStepper stepperR(AccelStepper::HALF4WIRE, motorRPin1, motorRPin3, motorRPin2, motorRPin4);

DifferentialStepper diffDrive(
    DifferentialStepper::HALF4WIRE,
    motorLPin1, motorLPin3, motorLPin2, motorLPin4,
    motorRPin1, motorRPin3, motorRPin2, motorRPin4
);

#define STEPS_PER_MM 5000/232
#define STEPS_PER_DEG 3760.0 / 180.0
#define WHEELSPACING 110

// equivalent to 1.8 * STEPS_PER_MM
#define STEPS_OF_BACKLASH   39

//LogoCommandQueue cmdQ(20);

// logobot state info
struct STATE {
  float x;
  float y;
  float ang;
  byte colliding;  // 0 = not colliding, 1=left, 2=right, 3=both
};
STATE state;

Servo penliftServo;

unsigned long buzzEnd = 0;

// buffered text to "write" using the pen
String text = "";

// cmd received over serial - builds up char at a time
String cmd;

//Logo::LogoParsedCommand lpc;

// position calcs
void resetPosition() {
  state.x = 0;
  state.y = 0;
  state.ang = 0;
}

void setup()
{
  Serial.begin(9600);
  Serial.println("Logobot");
  diffDrive.setMaxStepRate(1000);
  diffDrive.setAcceleration(666);
  diffDrive.setInvertDirectionFor(0,true);

  pinMode(switchFL, INPUT_PULLUP);
  pinMode(switchFR, INPUT_PULLUP);

  pinMode(InternalLED, OUTPUT);

  //pinMode(LEDRED, OUTPUT);
  //pinMode(LEDGREEN, OUTPUT);
  //pinMode(LEDBLUE, OUTPUT);

  penliftServo.attach(11);
  //penUp();

  //LogobotText::begin(cmdQ);

  pinMode(buzzer, OUTPUT);

  for (int i = 0; i < 3; i++) {
    digitalWrite(buzzer, HIGH);
    delay(100);
    digitalWrite(buzzer, LOW);
    delay(25);
  }

  resetPosition();
/*
  Logo::LogoParsedCommand cmd1;

  Logo::printProcedures();
  Logo::parseCommand("BK 50", &cmd1);

  Serial.println(cmd1.type);
  */

}

void loop()
{

    diffDrive.run();

    if (diffDrive.isQEmpty()) {
        Serial.println("Queuing move");
        diffDrive.queueMove(1000 + random(0,1000),1000 + random(0,1000));
    }
  /*
  // Parse Logo commands from Serial, add to cmdQ
  if (Serial.available()) {
    char c = Serial.read();
    if (c == '\r' || c == '\n') {
      if (cmd != "") {
        if (cmd == "STAT") {
          showStatus();
        } else if (cmdQ.isFull()) {
            Serial.println("BUSY");
        } else {
            if (cmd[0] == '!') {
                emergencyStop();
                cmdQ.insert(cmd.substring(1));
            } else {
                cmdQ.enqueue(cmd);
            }
            Serial.println("OK:" + cmd);
        }

        cmd = "";
      }
    } else {
      cmd += c;
    }
  }

  handleCollisions();

  // Do buzzer
  if (millis() < buzzEnd)
    digitalWrite(buzzer, HIGH);
  else
    digitalWrite(buzzer, LOW);

  // Let steppers run
  stepperL.run();
  stepperR.run();

  // Disable motors when stopped to save power
  // Note that AccelStepper.disableOutputs doesn't seem to work
  // correctly when pins are inverted and leaves some outputs on.
  if (stepperL.distanceToGo() == 0 && stepperR.distanceToGo() == 0) {

    if (cmdQ.isEmpty()) {

      // check the text writing buffer
      if (text.length() > 0) {
        char c = text[0];
        text = text.substring(1);  // lose the first character
        //LogobotText::writeChar(c, state.x, state.y);

      } else {
        // take a breather
        digitalWrite(motorLPin1, LOW);
        digitalWrite(motorLPin2, LOW);
        digitalWrite(motorLPin3, LOW);
        digitalWrite(motorLPin4, LOW);
        digitalWrite(motorRPin1, LOW);
        digitalWrite(motorRPin2, LOW);
        digitalWrite(motorRPin3, LOW);
        digitalWrite(motorRPin4, LOW);
      }
    } else {
      // pop and process next command from queue
      doLogoCommand(cmdQ.dequeue());
    }
  }
  */
}

/*
static void doLogoCommand(String c)
{

  if (c.startsWith("TO")) {
    // split out x and y co-ordinates
    int sp = c.indexOf(" ",3);
    driveTo(c.substring(3,sp).toFloat(), c.substring(sp+1).toFloat());
  } else if (c.startsWith("ARC")) {
    // split out x and y co-ordinates
    int sp = c.indexOf(" ",4);
    arcTo(c.substring(4,sp).toFloat(), c.substring(sp+1).toFloat());
  } else if (c.startsWith("FD")) {
    drive(c.substring(3).toFloat());
  } else if (c.startsWith("BK")) {
    drive(-c.substring(3).toFloat());
  } else if (c.startsWith("RT")) {
    turn(-c.substring(3).toFloat());
  } else if (c.startsWith("LT")) {
    turn(c.substring(3).toFloat());
  } else if (c.startsWith("ST")) {
    stop();
  } else if (c.startsWith("SE")) {
    emergencyStop();
  } else if (c.startsWith("BZ")) {
    buzz(c.substring(3).toInt());
  } else if (c.startsWith("PU")) {
    penUp();
  } else if (c.startsWith("PD")) {
    penDown();
  } else if (c.startsWith("FS")) {
	//LogobotText::setFontSize(c.substring(3).toFloat());
  } else if (c.startsWith("SIG")) {
    //writeText("Logobot");
  } else if (c.startsWith("WT")) {
    writeText(c.substring(3));
  } else if (c.startsWith("PQ")) {
    cmdQ.printCommandQ();
  }
}

void stop() {
  stepperL.stop();
  stepperR.stop();
}

void emergencyStop() {
  stepperL.setCurrentPosition(stepperL.currentPosition());
  stepperL.setSpeed(0);
  stepperR.setCurrentPosition(stepperR.currentPosition());
  stepperR.setSpeed(0);
}

void pushTo(float x, float y)
{
  String s = "TO ";
  s += x;
  s += " ";
  s += y;
  cmdQ.enqueue(s);
}

static void driveTo(float x, float y) {
  // calc angle
  float ang = atan2(y-state.y, x-state.x) * RADTODEG;
  // now angle delta
  ang = ang - state.ang;
  if (ang > 180)
    ang = -(360 - ang);
  if (ang < -180)
    ang = 360 + ang;

  turn(ang);

  // and distance
  float dist = sqrt(sqr(y-state.y) + sqr(x-state.x));
  String s = "FD ";
  s += dist;
  cmdQ.insert(s);
}

void drive(float distance)
{
  // update state
  state.x += distance * cos(state.ang * DEGTORAD);
  state.y += distance * sin(state.ang * DEGTORAD);

  // prime the move
  int steps = distance * STEPS_PER_MM;
  stepperL.move(steps);
  stepperR.move(steps);
}

void turn(float ang)
{
  // update state
  state.ang += ang;

  // correct wrap around
  if (state.ang > 180) state.ang -= 360;
  if (state.ang < -180) state.ang += 360;

  // prime the move
  int steps = ang * STEPS_PER_DEG;
  stepperR.move(steps);
  stepperL.move(-steps);
}


void arcTo (float x, float y) {

    if (y == 0) return;

    float cx1 = x - state.x;
    float cy1 = y - state.y;

    //v.rotate(degToRad(-this.state.angle));
    float ang = -state.ang * DEGTORAD;
    float ca = cos(ang);
    float sa = sin(ang);
    float cx = cx1 * ca - cy1 * sa;
    float cy = cx1 * sa + cy1 * ca;

    float m = -cx / cy;

    // calc centre of arc
    // from equation
    // y - y1 = m (x - x1)
    // rearranged to find y axis intersection
    // x = (-y1)/m + x1
    float x1 = -(cy/2.0) / m + (cx/2.0);

    float dl = 0, dr = 0;
    float targetAng;
    float cl, cr;

    if (x1 < 0) {
        targetAng = atan2(cy, -x1 + cx) * RADTODEG;

        cl = 2.0 * PI * (-WHEELSPACING/2.0 - x1);
        dl = cl * targetAng/360.0;

        cr = 2.0 * PI * (WHEELSPACING/2.0 - x1);
        dr = cr * targetAng/360.0;

    } else {
        targetAng = atan2(cy, x1 - cx) * RADTODEG;

        cl = 2.0 * PI * (x1 + WHEELSPACING/2.0 );
        dl = cl * targetAng/360.0;

        cr = 2.0 * PI * (x1 - WHEELSPACING/2.0);
        dr = cr * targetAng/360.0;
    }

    stepperL.move(dl * STEPS_PER_MM);
    stepperR.move(dr * STEPS_PER_MM);
}


void buzz(int len)
{
  buzzEnd = millis() + len;
}

void penUp()
{
  penliftServo.write(10);
}

void penDown()
{
  penliftServo.write(90);
}

static void writeText(String s) {
  // overwrite write text
  text = s;
  text.toUpperCase();

  // reset current state
  resetPosition();
}


long sqr(long v) {
  return v*v;
}
*/

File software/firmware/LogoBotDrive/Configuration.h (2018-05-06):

#ifndef Configuration_h
#define Configuration_h

// Pin definitions
// Left motor driver
#define MOTOR_L_PIN_1       2     // IN1 on the ULN2003 driver 1
#define MOTOR_L_PIN_2       3     // IN2 on the ULN2003 driver 1
#define MOTOR_L_PIN_3       4     // IN3 on the ULN2003 driver 1
#define MOTOR_L_PIN_4       5     // IN4 on the ULN2003 driver 1

// Right motor driver
#define MOTOR_R_PIN_1       6     // IN1 on the ULN2003 driver 1
#define MOTOR_R_PIN_2       7     // IN2 on the ULN2003 driver 1
#define MOTOR_R_PIN_3       8     // IN3 on the ULN2003 driver 1
#define MOTOR_R_PIN_4       9     // IN4 on the ULN2003 driver 1

// Piezo buzzer
#define BUZZER_PIN          10

// Microswitches
#define SWITCH_FL_PIN	    A0
#define SWITCH_FR_PIN	    A1
#define SWITCH_BL_PIN	    A2
#define SWITCH_BR_PIN	    A3

// LED
#define LED_RED_PIN         11
#define LED_GREEN_PIN	    12
#define LED_BLUE_PIN	    13

// PN532
#define PN532_SCK  (13)
#define PN532_MOSI (11)
#define PN532_SS   (10)
#define PN532_MISO (12)

#endif

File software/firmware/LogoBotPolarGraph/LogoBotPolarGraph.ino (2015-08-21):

#include "Configuration.h"
#include <DifferentialStepper.h>
#include <PolarBot.h>
#include <CommandQueue.h>
#include <LogobotText.h>
#include <Servo.h>

// left and right are inverted vs normal LogoBot wiring
// orientations are when looking at the drawing surface from the front
PolarBot bot(MOTOR_R_PIN_1, MOTOR_R_PIN_2, MOTOR_R_PIN_3, MOTOR_R_PIN_4, MOTOR_L_PIN_1, MOTOR_L_PIN_2, MOTOR_L_PIN_3, MOTOR_L_PIN_4);
CommandQueue cmdQ(15);
CommandQueue textQ(20);
String cmd; // cmd received over serial - builds up char at a time
float lineY;  //  stores current line position to allow for writing lines of text

void setup()
{
  Serial.begin(9600);
  Serial.println("Logobot Polar Graph");
  bot.begin();
  bot.initPenLift(SERVO_PIN);
  //bot.initBuzzer(BUZZER_PIN);
  bot.enableLookAhead(true);
  //bot.playStartupJingle();
  LogobotText::begin(textQ);

  // bot will initialise at 260,-300
  lineY = bot.state.y;
}

void loop()
{
  // Parse Logo commands from Serial
  if (Serial.available()) {
    char c = toupper(Serial.read());

    if (c == '\r' || c == '\n') {  // if found a line end
      if (cmd != "") {  // check the command isn't blank
        if (cmd == "STAT") { // handle status commands: execute immediately, no need to parse and/or queue
          showStatus();
        } else if (cmdQ.isFull()) {
            Serial.println("BUSY");
        } else {
            parseLogoCommand(cmd);
            Serial.println("OK:" + cmd);
        }

        // reset the command buffer
        cmd = "";
      }
    } else {
      cmd += c;  // append the character onto the command buffer
    }
  }

  // keep the bot moving (this triggers the stepper motors to move, so needs to be called frequently, i.e. >1KHz)
  bot.run();

  // dequeue commands from textQ, then cmdQ
  // textQ will be emptied before processing anything in cmdQ
  if (dequeueFrom(&textQ))
    dequeueFrom(&cmdQ);
}

static boolean dequeueFrom(CommandQueue *q) {
  if (!q->isEmpty()) {
    // see if we can queue the next command to the bot...  two situations where we can dequeue:
    //   1) if the next command is a movement command, and the bots motion queue isn't full
    //   2) the bot has finished whatever it was doing
    if (
        ( q->peekAtType() <= LOGO_MOVE_CMDS && !bot.isQFull() )
        ||
        ( !bot.isBusy() )
    ) {
        // dequeue and process next command - ultimately passing it over to the bot object for execution
        doLogoCommand(q->dequeue());
    }
  }
  // return true when this queue is empty
  return q->isEmpty();
}

static void showStatus()
{
  // Format: "X Y ang qSize"
  Serial.print((int)bot.state.x);
  Serial.print(',');
  Serial.print((int)bot.state.y);
  Serial.print(',');
  Serial.print((int)bot.state.ang);
  Serial.print(' ');
  Serial.print((int)bot.state.left);
  Serial.print(',');
  Serial.print((int)bot.state.right);
  Serial.print(' ');
  Serial.println(cmdQ.pending());
}


static void parseLogoCommand(String c) {
    // parse and queue/insert
    uint8_t cmdType = 0xff;

    // check for urgent commands
    boolean doNow = false;
    if (cmd[0] == '!') {
        doNow = true;
        c = c.substring(1);
    }

    // parse the command type
    if (c.startsWith("TO")) {
        cmdType = LOGO_CMD_TO;
    } else if (c.startsWith("ARC")) {
        cmdType = LOGO_CMD_ARC;
	} else if (c.startsWith("CIRC")) {
		cmdType = LOGO_CMD_CIRC;
    } else if (c.startsWith("FD")) {
        cmdType = LOGO_CMD_FD;
    } else if (c.startsWith("BK")) {
        cmdType = LOGO_CMD_BK;
    } else if (c.startsWith("RT")) {
        cmdType = LOGO_CMD_RT;
    } else if (c.startsWith("LT")) {
        cmdType = LOGO_CMD_LT;
    } else if (c.startsWith("ST")) {
        cmdType = LOGO_CMD_ST;
    } else if (c.startsWith("SE")) {
        cmdType = LOGO_CMD_SE;
    } else if (c.startsWith("BZ")) {
        cmdType = LOGO_CMD_BZ;
    } else if (c.startsWith("PU")) {
        cmdType = LOGO_CMD_PU;
    } else if (c.startsWith("PD")) {
        cmdType = LOGO_CMD_PD;
    } else if (c.startsWith("PF")) {
        cmdType = LOGO_CMD_PF;
    } else if (c.startsWith("FS")) {
        cmdType = LOGO_CMD_FS;
    } else if (c.startsWith("SIG")) {
        cmdType = LOGO_CMD_SIG;
    } else if (c.startsWith("WT")) {
        cmdType = LOGO_CMD_WT;
    } else if (c.startsWith("PQ")) {
        cmdType = LOGO_CMD_PQ;
    } else if (c.startsWith("CS")) {
		    cmdType = LOGO_CMD_CS;
	  } else if (c.startsWith("NL")) {
        cmdType = LOGO_CMD_NL;
    }

    // give up if command not recognised
    if (cmdType == 0xff) return;

    // lose the command name, keep the parameters
    int sp = c.indexOf(' ');
    if (sp > -1) {
        c = c.substring(sp+1);
    } else {
        c = "";
    }

    // insert/queue the command
    if (doNow) {
        bot.emergencyStop();  // stop the bot, clear any internally queued movement commands
        cmdQ.insert(c, cmdType);  // insert the new command at the head of the command queue
    } else {
        cmdQ.enqueue(c, cmdType);
    }

    // debug what bot is up to
    /*
    Serial.print("CQ Peek: ");
    Serial.println(cmdQ.peekAtType());
    Serial.print("bot.isQFull:");
    Serial.println(bot.isQFull());
    */
}
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

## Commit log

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2014-10-16 Noddy nut and bolt library. I'm assuming we'll replace this with something else.
    [BoltLibrary.scad, BoltTest.scad]
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2014-10-17 Rename BoltLibrary -> Bolt. Move demo into sandbox.
    [Bolt.scad, BoltDev.scad, BoltTest.scad]
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2014-10-19 Initial commit of Arduino Pro Mini/Micro vitamin
    Todo: All features other than header holes
    [ProMicro.scad]
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2014-10-19 Up issued the version number.
    [MicroSwitch.scad]
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2014-10-19 Add clearance area for board components
    [ProMicro.scad]
2014-10-19 exploring Jamie's ProMicro bug
    [ProMicroDebugging.scad]
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2014-10-22 ULN2003 Driver board - add some connectors - moved variables out to be global so they can be used in the connectors - tidied up the formatting a bit
    [StepperDriverBoardDev.scad, ULN2003DriverBoard.scad]
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2014-10-22 binding to moreShapes
    [moreShapes.scad, utils.scad]
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2014-10-23 Added Breadboard views and corrected attach bug
    [Breadboard.scad, BreadboardAssembly.scad, attach.scad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]
2014-10-23 Removed detailed BOM table
    Summary BOM table was getting too wide!
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2014-10-23 Fix marble view and rebuild
    [Marble.scad, temp.scad]
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2014-10-23 UpperCamelCase module name, Reduce $fn levels and removed prefix on local parameter names
    [LogoBot.scad, MicroSwitch.scad, MicroSwitchDev.scad]
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2014-10-24 Reworked STL view rendering
    [BasicShell_STL.scad, LogoBot.scad, LogoBotBase_STL.scad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]
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2014-10-25 finished ribbonCable module, added to wheel
    not final, but illustrates the capability
    [LogoBot.scad, LogoBotAssembly.scad, Wheel.scad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]
2014-10-25 fixed non-manifold issue with motor clips
    [LogoBot.scad, LogoBotBase.scad, LogoBotBase.stl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]
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2014-10-25 Correcting Explode var name
    [Breadboard.scad, BreadboardAssembly.scad, LogoBot.scad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]
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2014-10-26 Corrected bug in OpenSCAD 2014.10
    [BreadboardAssembly.scad, config.scad]
2014-10-26 Add enums for arduino pro model variants
    - Add headerless example to the sandbox
    - Adjust Breadboard assembly to match
    [ArduinoPro.scad, ArduinoProDev.scad, Breadboard.scad]
2014-10-26 Add header pins (optionally) to ArduinoPro models
    - Also show pins in Breadboard assembly
    [ArduinoPro.scad, ArduinoProDev.scad, Breadboard.scad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]
2014-10-26 Only show minimum clearance with no header pins
    [ArduinoPro.scad, ArduinoProDev.scad]
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2014-10-26 Add some break-away material for headers
    todo: rotate material location based on vector
    [ArduinoPro.scad]
2014-10-26 Whitespace fixes following tab un/expand
    [ArduinoPro.scad]
2014-10-26 Fix serial header holes not being drawn
    [ArduinoPro.scad]
2014-10-27 Add some components to the ArduinoPro
    - Approximate locations; only main components shown
    [ArduinoPro.scad]
2014-10-27 A couple more whitespace fixes
    [ArduinoPro.scad]
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2014-10-27 Dirty hack for rotation of header material
    FIXME: material needs to be rotated based on vector argument
    [ArduinoPro.scad]
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2014-10-28 Fixed bug in supplementary module pattern
    [static.py]
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2014-10-28 build fixes
    [BreadboardAssembly_Step1.scad, LogoBot.scad, LogoBotAssembly_Step1.scad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]
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2014-10-28 Remove no longer needed clearance box
    [ArduinoPro.scad, ArduinoProDev.scad]
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2014-10-28 Flip the alternate batteries
    [BatteryPack.scad]
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2014-10-28 Whitespace fixes for MicroUSB vitamin
    [MicroUSB.scad]
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2014-10-29 Oops, names of enums fixed
    [BatteryPack.scad, LogoBot.scad]
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2014-10-30 reworking bon system to use json
    [assemblies.scad, config.scad, damian_playground2.scad]
2014-10-30 LED Enhancements - allow multiple sizes - add optional legs - optional color parameter - RGB led model - adopt "enum style" - some convenience helper functions to make enum style easier for end users
    [LED.scad, LedDev.scad, ULN2003DriverBoard.scad]
2014-10-30 reworked to use json
    [Breadboard.scad, JumperWire.scad, LogoBot.scad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]
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2014-10-31 Nicer looking PCB headers (code stolen from Arduino lib and modified slighly) Connectors for PCB headers
    [LogoBot.scad, ULN2003DriverBoard.scad]
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2014-11-01 Some cooler looking wheels that also use use less plastic to print
    [Wheel.scad, WheelAssembly.scad]
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2014-11-02 Extend central hub to length of motor shaft and add 3mm grub screw hole
    [LogoBotAssembly.scad, Wheel.scad]
2014-11-02 added syntax error debug
    [LogoBot.scad, assemblies.scad]
2014-11-02 testing multiple machines
    TODO: fix bug with part counts
    [LogoBot.scad, LogoBotScribbler.scad]
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2014-11-02 Move render() call to fix rending issues
    [Wheel.scad]
2014-11-02 fixed some minor BOM bugs and enhanced docs
    [LogoBotScribbler.scad, assemblies.scad, fakeGroundShadow.scad]
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2014-11-03 corrected assembly view directories
    fixes bug with multiple machine assembly views overwriting each other
    [assemblies.py, guides.py]
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2014-11-04 updated ci and utils
    fixed a bunch of minor bugs
    [attach.scad, config.scad, moreShapes.scad]
2014-11-04 correcting module misname
    [moreShapes.scad]
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2014-11-05 Fix bugs created while editing blind last week - BatteryPack_AA now exists as an enum (no others yet) Connection point exists but as-yet untested Added own "eta" so don't have to include whole univer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
    [BatteryPack.scad, BatteryPackDev.scad]
2014-11-05 Fixed syntax error created when de-conflicting main logobot assembly
    [LogoBot.scad]
2014-11-05 Fix openscad module to find lower-cased binary names too
    [openscad.py]
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2014-11-24 Double wheel thickness from 2mm to 4mm (also needed a fix to the hub so the grub screw hole didn't get partly filled in)
    [Wheel.scad, machine.scad]
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2014-11-26 Udpdate motor vitamin with corrected dimensions
    [Wheel.scad, motor.scad, motorDev.scad]
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2014-11-27 Option to disable shell for use in sandbox so you can see what is placed where
    [LogoBot.scad, LogoBotAssembly.scad]
2014-11-27 Base: remove rogue translate so that wheels are in the centre or the wheel slots again
    [LogoBotBase.scad]
2014-11-27 Diagnosing build error
    [LogoBot.scad, motor.scad, printedparts.scad]
2014-11-30 Added a Snap Pin utility.
    [PinsDev.scad, pins.scad, utils.scad]
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2014-12-05 Fixed typo in PinsDev.scad in Sandbox.
    [PinsDev.scad]
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2014-12-11 Better microswitch holders giving more ground clearance
    [Bumper.scad, BumperDev.scad, LogoBot.scad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]
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2014-12-11 Position Microswitches correctly in main model
    [LogoBot.scad]
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2014-12-11 More tidyup, realistically you don't mirror the bumper to put in on, you rotate it.
    [BumperDev.scad, LogoBot.scad]
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2014-12-15 fixed minor bug in guides.py
    missing markdown parameter crashing guide generation - shshouldn't
    occur, but did!
    [guides.py]
2014-12-15 fixing bug caused by new OpenSCAD version
    [Wheel.scad]
2014-12-17 rebuild
    images are smaller than intended due to bug with newer version of
    OpenSCAD… :(
    [Bumper.scad, Bumper.stl, MicroServo_Body.stl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]
2014-12-17 rebuild
    tweaked the step instructions for the bumper assembly to remove the
    newline - doesn't parse correctly with new version of OpenSCAD
    [Bumper.scad, temp.scad]
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2015-06-09 Add a flange to the bottom of the bumper to make it a bit stiffer. Should help with direct contacts on the front
    [Bumper.scad]
2015-06-23 Modified bumper springs
    Now generated by bezier curves to make alterations more flexible and
    intuitive… hopefully springier during head-on collisions
    [BasicShell.stl, Bumper.scad, Bumper.stl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]
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2015-07-06 A clip using the pins system to directly attach a pro mini
    [ProMiniClip.scad, printedpart_ProMiniClip.scad, printedparts.scad]
2015-07-09 Create a bumper stabiliser to hold it steady when bumped and make the contact with the microswitches more reliable
    [Bumper.scad, BumperDev.scad, BumperStabiliser.scad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]
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2015-07-19 Pen lift assembly and rough integration into the scribbler version of the LogoBot
    [LogoBot.scad, LogoBotScribbler.scad, PenLift.scad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]
2015-07-23 Update LogoBotWifiScribbler.ino
    Reworked to include command queue, added "TO" command and internal tracking of position/angle in cartesian co-ord frame
    [LogoBotWifiScribbler.ino]
2015-07-23 Update LogoBotWifiScribbler.ino
    Corrected bug in driveTo()
    [LogoBotWifiScribbler.ino]
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2015-07-23 Fix up issues with pushTo() inserting too many spaces which causes future parsing of the command to fail
    [LogoBotWifiScribbler.ino]
2015-07-24 Better collision handling
    proper collision handler... inserts appropriate recovery actions onto cmdQ
    [LogoBotWifiScribbler.ino]
2015-07-24 Optimise turn to take the shortest angle
    [LogoBotWifiScribbler.ino]
2015-07-24 More distinctive startup chirp (useful when batteries go flat and it resets itsself)
    [LogoBotWifiScribbler.ino]
2015-07-24 Decrease repetition in collision, additional comment to clarify wierd looking order of action
    [LogoBotWifiScribbler.ino]
2015-07-24 Backlash support
    Added basic backlash support to AccelStepper library and LogoBot
    [LogoBotWifiScribbler.ino]
2015-07-24 Fix for emergencyStop
    sets speed to zero to correct odd behaviour with !ST
    [LogoBotWifiScribbler.ino]
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2015-07-26 Fix bug in arcTo()
    Fixed bug in arcTo within the rotate vector stage (lines 444-448)
    [LogoBotWifiScribbler.ino]
2015-07-26 Bumper and arcTo fix
    [LogoBotWifiScribbler.ino]
2015-07-26 Better DNS Server implementation that works on Windows, Android and IOS. Can probably be replaced with the ESP8266 DNSServer lib once they fix it.
    [LogoBotEsp8266.ino]
2015-07-27 Move webpage into separate file for clarity and to hopefully fix intermittent compile / parse bug in Arduino IDE
    [LogoBotEsp8266.ino, WebPages.h]
2015-07-31 Convert LogobotText to use namespaces (~=static class) to claw back some program memory. Works nicely, and you there's no longer any need to define letter functions as 'static'
    Only drawback, you need to call functions with a double colon rather than a dot which isn't very "Arduino" - eg LogobotText::begin(...), LogotbotText::writeChar(...)
    Before:
    Binary sketch size: 28,616 bytes (used 93% of a 30,720 byte maximum) (1.36 secs)
    Minimum Memory Usage: 587 bytes (29% of a 2048 byte maximum)
    After:
    Binary sketch size: 24,756 bytes (used 81% of a 30,720 byte maximum) (0.92 secs)
    Minimum Memory Usage: 587 bytes (29% of a 2048 byte maximum)
    [LogoBotWifiScribbler.ino]
2015-07-31 Started on a StealthShell
    …didn’t get very far
    [StealthShell.scad]
2015-07-31 Fix compiler warning about type comparison
    [LogoBotWifiScribbler.ino]
2015-08-01 Integrating pins into build system
    which involves adding a suitable printedPart() call
    [pins.scad]
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2015-08-01 bumper stabilisers now building correctly
    [BumperStabiliser.stl, LogoBot.scad, pins.scad]
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2015-08-03 Revert, doesn't build via Arduino IDE. (reverted from commit 108d592f769578046cdb46d14d77719ba9d219fd)
    [LogoBotWifiScribbler.ino]
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2015-08-04 Updated ci scripts plus test rebuild
    Updated ci scripts (and associated utils/assemblies.scad) to latest
    versions from OpenSCAD_Machine_Design_Template project
    [BumperStabiliser.stl, MicroServo_Body.stl, MicroServo_Spline.stl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]
2015-08-04 Added basic Mini Toggle Switch vitamin
    parameterised, but only single type defined - SPST6A
    [MiniToggleSwitch.scad, vitamin_MiniToggleSwitch.scad, vitamins.scad]
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2015-08-04 Tweaks to pin tack printed part and rebuild
    reducing parameter set into pintack_STL, ahead of harmonising lengths
    across the model
    [LogoBot.scad, PinTack.scad, PinTackH141.stl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]
2015-08-04 Variable renames Type changes (save a ~150bytes or program space and 13bytes of ram)
    [Configuration.h]
2015-08-04 Switch back to int for buzz() function
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2015-08-04 Tweak instructions, refine guides.py
    Guides.py no longer generates Assembly stages that have zero steps
    (e.g. where conditional steps cause a sub-assembly to be redundant)
    [LogoBot.scad]
2015-08-04 Added vitamin definitions to missing parts, rebuild
    Arduino Pro, MicroSwitch, Motor and ULN2003DriverBoard now correctly
    incorporated into assembly guides
    [ArduinoPro.scad, MicroSwitch.scad, ULN2003DriverBoard.scad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]
2015-08-04 OptionalExtras dummy machine and simple base
    Added an OptionalExtras.scad machine for collecting misc optional parts
    or variants. Have included a simplified/minimalistic base as an
    example.
    [OptionalExtras.scad, SimpleBase.scad, SimpleBase.stl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]
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2015-08-04 Update Penlift servo to use A4, one of the "extra" io pins A6/7 are analog (in?) only
    [Configuration.h]
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2015-08-05 Tweaks to BatterPack
    Added vitamin support. Calls to Battery are now encapsulated.
    [Battery.scad, BatteryPack.scad, BatteryPackDev.scad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]
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2015-08-05 Stop bot getting stuck in corners
    [LogoBotWifiScribbler.ino]
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2015-08-05 Wired up rear switches
    also fixed colour of ULN2003 pcb
    [LogoBot.scad, ULN2003DriverBoard.scad]
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2015-08-05 Fix bug in ULN2003
    nested vitamins (LEDs) not correctly wrapped in ULN2003 vitamin
    statement
    [ULN2003DriverBoard.scad]
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2015-08-05 Added hook and loop tape vitamin
    to hold battery pack onto base
    [HookAndLoopTape.scad, LogoBot.scad, vitamin_HookAndLoopTape.scad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]
2015-08-05 Fix busy bug in Wifi batch page
    [WebPages.h]
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2015-08-06 Major rework of command parsing
    Command type now parsed before adding to the command queue, only
    parameters are stored as strings. Bunch of minor optimisations
    included.
    [Configuration.h]
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2015-08-06 Corrected MotorClip for new driver boards
    Latest drivers board are >2mm wider
    [MotorClip.scad, ULN2003DriverBoard.scad, printedpart_MotorClip.scad]
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2015-08-06 Avoiding single character strings
    [LogoBotWifiScribbler.ino]
2015-08-07 Bug fixes
    Fixes:
    Correctly parses parameter values for single parameter commands.
    bot.isQFull() implements correct logic - allows movement commands to
    queue in bot, freeing main cmdQ
    [LogoBotWifiScribbler.ino]
2015-08-07 Update bumper, diff springs
    Altered the springs to try and improve frontal contacts
    [Bumper.scad, Bumper.stl, BumperStabiliser.stl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]
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2015-08-07 Updated lid
    Includes:
    - Swindon Hackspace logo
    - Fitting tolerance (0.5mm)
    [Lid.scad, Lid.stl, snhack_logo_h.stl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]
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2015-08-07 Playing with voronoi shell
    Rob’s idea… messing with getting something that looks cool and is
    printable
    [VoronoiShell.scad, utils.scad, voronoi.scad]
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2015-08-08 Fix up bumper issues
    [LogoBotWifiScribbler.ino]
2015-08-08 New logo command CS - Clear Screen, resets position state
    [Configuration.h]
2015-08-08 No longer need to hold onto stepper pins in bot because Diffdrive correctly disables outputs.
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2015-08-09 Faster voronoi type 2, fixed lid opening
    [VoronoiShell.scad]
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2015-08-09 Tweak tolerances
    added 0.5mm
    [LineSensorHolder.scad]
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2015-08-10 Added buzzer to basic firmware
    [LogoBotBasic.ino]
2015-08-10 Increased size of bumper bumpstop
    To make bumper/microswitch easier and more tolerant to being bent out
    of alignment… might also avoid need for bumper stabiliser - subject to
    testing
    [Bumper.scad]
2015-08-10 Added a little extra clearance for motor depth
    To make press fitting the motors easier for kids
    [MotorClip.scad]
2015-08-11 Bug fix for removing orphaned STLs
    [MotorClip.stl, Pintack.stl, PintackH141BH2.stl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]
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2015-08-12 bugfix on planner initialisation
    lastDirBits incorrectly interpreted for head of queue… also removed
    individual planner flag on command blocks (not used/required)
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2015-08-12 Revamp of guide generation and various bug fixes
    [Base.stl, BasicShell.scad, Lid.scad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]
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2015-08-13 Tweaks to diff stepper
    trying to isolate bug in look ahead planning
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2015-08-15 Fix up connectors, etc.
    [LidIR.scad, printedpart_LidIR.scad]
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2015-08-15 Add motor reverse option to bot.begin()
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2015-08-15 Switch back to active buzzer. Passive buzzer on pin 10 + servo doesn't work.
    [LogoBotIRSeeker.ino]
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2015-08-19 bug fix for multiple WT commands
    [LogoBotPolarGraph.ino]
2015-08-19 Fix for multiple WT commands
    [LogoBotWifiScribbler.ino]
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2015-08-20 Fix for no slic3r install
    [slic3r.py]
2015-08-20 Apply fixes from polargraph
    [LogoBotWifiScribbler.ino]
2015-08-20 Correct-case filenames for Linux build
    [Lid.scad, screw.scad, vitamins.scad]
2015-08-21 Bug fix for non-mac platforms
    [build.py]
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2015-08-22 Integrated spiro page into ESP firmware
    Needs thorough testing - memory usage is high, so may make the whole
    thing unstable
    [LogoBotEsp8266.ino, WebPages.h]
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2015-08-26 Fixes for spiro and draw pages
    [WebPages.h]
2016-04-23 LogobotRemoteControlled version 1. See Robot Remote code on the SwindonMakerspace wiki for the remote controller code
    [Configuration.h]
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
